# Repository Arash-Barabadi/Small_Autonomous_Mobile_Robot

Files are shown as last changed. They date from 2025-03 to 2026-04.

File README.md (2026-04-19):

# Small Autonomous Mobile Robot
### The first challenge is budgeting. I have already designed an architecture for a teleoperated car using ROS2 on a Jetson Orin NX, which is straightforward since the Jetson provides a powerful computing platform for compiling and executing all necessary code.
### To reduce costs, I opted to use a ESP32 as my main microcontroller, which costs only about €5 instead of €800!  The main limitation of the ESP32 is its lack of direct support for ROS2. However, it does support micro-ROS. Therefore, I decided to implement all the code within the micro-ROS framework.

[🎥 Watch my project demo on YouTube](https://www.youtube.com/watch?v=UUFdapDHFw0)



Robot_1st

Robot_2nd

# Networking (ESP32 ↔ ROS 2 PC)

## A guide how to intall micro-ros agent in our system is as follows:
## https://cps.unileoben.ac.at/install-micro-ros-on-esp32/
## This robot uses micro-ROS over WiFi (UDP). The ESP32 connects to a WiFi network and sends ROS 2 messages to the micro-ROS agent running on the PC.
## Architecture
### ESP32 publishes: /scan, /imu/data, /wheel_ticks, ....
### ESP32 subscribes: /cmd_vel, ...
### PC runs: micro_ros_agent (UDP on port 8888)
### Transport: WiFi UDP (udp4)
### Requirements: 1- ESP32 and PC must be on the same network, 2- ESP32 must be able to reach the PC IP, 3- Port 8888/UDP must not be blocked by firewall
## Home WiFi Setup (Router Network)
## A- (Microcontroller Side) ESP32 config

### Find PC IP: On Ubuntu:

```bash
ip a
```

### Note: Use the inet ... address under WiFi interface (usually wlp, e.g. inet 10.126.78.187/24 brd 10.126.78.255 scope global dynamic noprefixroute wlp0s20f3). Example output:
```bash
inet 10.126.78.187/24 brd 10.126.78.255 scope global dynamic noprefixroute wlp0s20f3
```
### In main.cpp:
```cpp
char ssid[]     = "YOUR_WIFI_NAME";
char password[] = "YOUR_WIFI_PASSWORD";
IPAddress agent_ip(10, 126, 78, 187);   // PC IP on the same WiFi
const uint16_t agent_port = 8888;
```

## B- (PC side) Start micro-ROS agent
```bash
ros2 run micro_ros_agent micro_ros_agent udp4 --port 8888
```

Verify through :
```bash
ros2 topic list
ros2 topic echo /scan --once
```

# TF:



## System Overview
### Sensors & Sources
#### - Wheel encoders → wheel odometry node → /odom + odom → base_link TF
#### - LD14P LiDAR → micro-ROS → /scan (frame_id: base_laser)
### Static TF:
#### - base_link → base_laser
#### - base_link → imu_link
## SLAM
###  Package: slam_toolbox
###  Mode: online_async
### Frames: map → odom → base_link → base_laser

## Terminal Commands Used (ubuntu)
### 1- Start the micro-ROS Agent (UDP over Wi-Fi)
```bash
ros2 run micro_ros_agent micro_ros_agent udp4 --port 8888
```
### 2- Teleoperation - We can drive it with the standard ROS 2 keyboard teleop that publishes geometry_msgs/Twist (think of it like format of coommand) on /cmd_vel, our robot will subscribe to /cmd_vel (think of it like the channel where the command is sent) and moves accordingly. 

```bash
ros2 run teleop_twist_keyboard teleop_twist_keyboard
```
### 3- Static Transforms
#### Base  → Lidar (unit meter, radian)

```bash
ros2 run tf2_ros static_transform_publisher   --x 0 --y 0 --z 0.04125   --roll 0 --pitch 0 --yaw 0   --frame-id base_link --child-frame-id base_laser
```
#### Base → IMU (unit meter, radian)

```bash
ros2 run tf2_ros static_transform_publisher --x -0.0674 --y 0.006355 --z -0.0053 --roll 0 --pitch 0  --yaw -1.57 --frame-id base_link --child-frame-id imu_link
```
### 4- Wheel Odometry Node

```bashr
ros2 run wheel_odometry wheel_odometry_node
```

### 5- SLAM (slam_toolbox)
```bash
ros2 launch slam_toolbox online_async_launch.py slam_params_file:=/home/$USER/ros2_ws/src/wheel_odometry/config/slam_params.yaml
```
### 6- RVIZ

```bash
rviz2 -d /opt/ros/jazzy/share/nav2_bringup/rviz/nav2_default_view.rviz
```
### 7- Navigation
```bash
// ros2 launch nav2_bringup navigation_launch.py use_sim_time:=false params_file:=/home/$USER/ros2_ws/src/wheel_odometry/config/nav2_params.yaml
ros2 launch wheel_odometry navigation.launch.py map:=/home/arash/ros2_ws/maps/test_map.yaml

ros2 topic pub --once /initialpose geometry_msgs/msg/PoseWithCovarianceStamped "{
  header: {frame_id: 'map'},
  pose: {
    pose: {
      position: {x: 0.0, y: 0.0, z: 0.0},
      orientation: {z: 0.0, w: 1.0}
    },
    covariance: [0.25, 0.0, 0.0, 0.0, 0.0, 0.0,
                 0.0, 0.25, 0.0, 0.0, 0.0, 0.0,
}"}              0.0, 0.0, 0.0, 0.0, 0.0, 0.5]

```

# Challenges
## Challenges accomplished
## __ Pure rotation fix __

### During testing, the robot could move forward and turn while moving, but it could not rotate in place with a pure angular command like:

```bash
ros2 topic pub /cmd_vel geometry_msgs/msg/Twist "{linear: {x: 0.0}, angular: {z: 2.0}}" -r 5
```
### Interestingly, rotation worked as soon as a very small forward velocity was added, for example:

```bash
ros2 topic pub /cmd_vel geometry_msgs/msg/Twist "{linear: {x: 0.02}, angular: {z: 2.0}}" -r 5
```
### This showed that the issue was not in ROS 2 communication, but in the drivetrain behavior: pure in-place rotation was not overcoming static friction.
### Fix: A small internal linear assist was added inside cmdVelCallback() for pure rotation commands, before deadzone compensation:
``` cpp
if (fabsf(v) < 0.001f && fabsf(w) > 0.0f) {
  v = ROTATION_ASSIST_LINEAR;
}

v = compensateLinearDeadzone(v);
w = compensateAngularDeadzone(w);
```
### with
``` cpp
static constexpr float ROTATION_ASSIST_LINEAR = 0.02f;
```
### Result : After this change, pure rotation worked reliably.

## __ Watch dog __
## My first aim is to drive the robot over Wi-Fi communication between my laptop and the ESP32. I’ll use PlatformIO for building, testing, and deploying code on the ESP32, as it is a better alternative to the Arduino IDE. PlatformIO is installed on VS Code.

### 1- Originally, the robot continued moving indefinitely if no new /cmd_vel message was received (for example, when the Wi-Fi connection dropped or the teleop node stopped). This caused unsafe behavior — the last velocity command remained active and the robot kept accelerating or turning without control. 
### To solve this, a command timeout WATCHDOG was implemented. It continuously checks the time since the last received command and automatically stops both motors if no new command arrives within 250 ms as below:
```cpp
// =============== Update timestamp whenever a command arrives ========================
void cmdVelCallback(const void *msgin) {
  
  // at first update and record timestamp as soon as receiving a message
  last_cmd_us = micros();  // micros() returns the current time in microseconds

  //The incoming message is cast to a geometry_msgs::msg::Twist type
  const auto *msg = (const geometry_msgs__msg__Twist *)msgin;

  float v = constrain(msg->linear.x  / MAX_V, -1.0f, 1.0f);
  float w = constrain(msg->angular.z / MAX_W, -1.0f, 1.0f);

  float left_norm  = (v - w * TRACK / 2.0f) * K_LEFT;
  float right_norm = (v + w * TRACK / 2.0f) * K_RIGHT;

  setMotor(L_IN1, L_IN2, 0, speedToPwm(left_norm));
  setMotor(R_IN1, R_IN2, 1, speedToPwm(right_norm));
}
// ================== Check timeout each loop ======================
void checkCmdTimeout() {
  uint32_t now = micros();
  if (last_cmd_us && (now - last_cmd_us > CMD_TIMEOUT_US)) {
    safetyStop();
  }
}

```

### 2- The LD14P LiDAR outputs scan data using a clockwise angle convention and a left-handed coordinate system, which does not match the ROS REP-103 standard (counter-clockwise, right-handed). This mismatch caused mirrored scans and incorrect visualization in RViz and SLAM. To fix this, the LiDAR angle interpretation was corrected directly inside main.cpp on the ESP32 instead of trying to compensate with TF. Each raw LD14 angle is converted using θ_ros = −θ_ld14, ensuring the scan follows the ROS counter-clockwise convention. The LaserScan beam indexing and angle range were also updated to [-π, π], allowing the LiDAR to behave like a standard ROS sensor while TF now only represents the physical mounting of the LiDAR.
```cpp
/// The scan was redefined to cover a full ROS-style range:
static constexpr float ANGLE_MIN_RAD = -PI;
static constexpr float ANGLE_MAX_RAD =  PI;
static constexpr float ANGLE_INC_RAD = (2 * PI) / SCAN_BEAMS;
/// Added helper function for angle conversion
/// This performs the critical transformation: clockwise  → counter-clockwise & left-handed → right-handed
static inline float ld14DegToRosRad(float angle_deg_ld14)
{
    float angle_rad_ld14 = angle_deg_ld14 * DEG2RAD;
    float angle_rad_ros  = -angle_rad_ld14;
    return wrapToPi(angle_rad_ros);
}
/// Inside lidarSpinOnce() each raw LD14 point is converted before assigning it to a LaserScan beam:
float angle_rad_ros = ld14DegToRosRad(angle_deg_ld14);

float beam_f = (angle_rad_ros - ANGLE_MIN_RAD) / ANGLE_INC_RAD;
int beam = lroundf(beam_f);

/// Unobserved scan beams are filled with INFINITY:

scan_ranges[i] = INFINITY;

```

### https://www.linkedin.com/posts/prof-dr-ing-lars-n-josler-b35999161_robotics-engineering-opensource-share-7448631464512032768-y-hW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

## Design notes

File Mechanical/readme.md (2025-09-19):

# Caster Wheel Spacer
### as the robot needs to be stable, it's decks are requred to be parrallel to the ground. For this I needed to design a simple spacer beteen caster wheel and the deck to compensate this height difference:
### The 3D printed spacer:


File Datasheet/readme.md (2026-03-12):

## Slam explanation:

## https://husarion.com/tutorials/ros2-tutorials/8-slam/

## Some guides:
## https://micro.ros.org/
## https://robofoundry.medium.com/
## https://robofoundry.medium.com/building-cheapest-ros2-robot-using-esp32-part-1-hardware-build-af0044de68ce

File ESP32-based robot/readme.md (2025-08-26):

## ESP32S_WROOM-32



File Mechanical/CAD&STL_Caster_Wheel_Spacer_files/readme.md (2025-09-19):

# Caster Wheel Spacer
### As the robot needs to be stable, its decks must be parallel to the ground. For this, I designed a simple spacer between the caster wheel and the deck to compensate for the height difference.


### The 3D printed spacer:


### Before using spacer:


### After using spacer:


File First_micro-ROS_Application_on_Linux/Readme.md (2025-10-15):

# Step 1: Install ROS 2 and micro-ROS Build System
# Micro-ROS 
## The ROS framework, which can be considered quite large, needs to be brought onto the microcontroller. This goal can be achieved using the micro-ROS framework, which my robot is based on.
### ROS2 installation: 
### Please refer to the following website: https://docs.ros.org/en/foxy/Installation/Ubuntu-Install-Debians.html for installing ROS2 humble.
### Micro-Ros installation: 
### 1- Source the ROS 2 installation
```bash 
source /opt/ros/$ROS_DISTRO/setup.bash
```
### 2- Create a workspace and download the micro-ROS tools
```bash
mkdir microros_ws
cd microros_ws
git clone -b $ROS_DISTRO https://github.com/micro-ROS/micro_ros_setup.git src/micro_ros_setup
```

### 3- Update dependencies using rosdep
```bash
sudo apt update && rosdep update
rosdep install --from-paths src --ignore-src -y
```

### 4- Install pip
```bash
sudo apt-get install python3-pip
```

### 5- Build micro-ROS tools and source them
```bash
colcon build
source install/local_setup.bash
```
# Step 2: Understand the micro-ROS Build System Workflow

## The micro-ROS build system consists of four steps:

###    1-Create – Downloads required code repositories and cross-compilation toolchains.
#### ***Cross-compilation is the process of compiling code on one system (the host: Our Computer) to run on a different system (the target:here Raspberry Pi Pico) that may have a different architecture, operating system, or environment.***

##### For example: You write and compile code on your Ubuntu PC (x86_64).The compiled binary is meant to run on a microcontroller (Raspberry Pi Pico).

### Since the microcontroller may lack the necessary resources (CPU, memory, OS) to run a full compiler, cross-compilation allows you to generate compatible binaries on your powerful development machine.

###    2-Configure – Selects the app, transport method, and agent details.
###    3-Build – Cross-compiles the selected app.
###    4-Flash – Installs the compiled binaries on the hardware.

# Step 3: Create a Firmware Workspace

## Create the firmware workspace:
```bash
ros2 run micro_ros_setup create_firmware_ws.sh host
```
### A new firmware/ folder is created, containing:

###    main.c: Application logic & CMakeLists.txt: Compilation script

# Step 4: Configure the Ping Pong Application

##    Locate the built-in ping_pong app:
```bash
microros_ws/src/uros/micro-ROS-demos/rclc/ping_pong
```

### The app has two publisher-subscriber pairs:

###    A ping publisher sends unique ping messages.
###    A ping subscriber listens for external pings.
###    A pong publisher responds when a ping is received.

# Step 5: Build the Firmware

## Since micro-ROS is running on Linux (not a microcontroller), no cross-compilation is needed. Build the firmware:
```bash
ros2 run micro_ros_setup build_firmware.sh
source install/local_setup.bash
```
# Step 6: Create and Build the micro-ROS Agent

##    Download the micro-ROS agent packages:
```bash
ros2 run micro_ros_setup create_agent_ws.sh
```
## Build the agent:
```bash
ros2 run micro_ros_setup build_agent.sh
source install/local_setup.bash
```

### What is the micro-ROS Agent? 🤖📡

#### The micro-ROS Agent is like a translator or middleman between micro-ROS nodes (running on tiny devices or a Linux system) and the main ROS 2 network.
#### 🔹 Role of micro-ROS Agent

####    Microcontrollers (tiny computers) can't directly communicate with a full ROS 2 system.
####    The micro-ROS Agent acts as a bridge between:
####        micro-ROS nodes (running on embedded devices or Linux).
####        ROS 2 nodes (running on a standard computer).
####    It receives messages from micro-ROS nodes and forwards them to ROS 2, and vice versa.

#### 💡 Think of it like an interpreter 🗣️
#### Imagine a person speaking English (ROS 2) and another speaking Spanish (micro-ROS). The micro-ROS Agent is the interpreter who helps them understand each other.

# Step 7: Run the micro-ROS Application

##    Start the micro-ROS agent:
```bash
ros2 run micro_ros_agent micro_ros_agent udp4 --port 8888
```
## Open another terminal and start the micro-ROS node:
```bash
source /opt/ros/$ROS_DISTRO/setup.bash
source install/local_setup.bash
export RMW_IMPLEMENTATION=rmw_microxrcedds
ros2 run micro_ros_demos_rclc ping_pong
```

# Step 8: Test the Application
##  8.1 Verify the Ping Messages

##  Now, we want to check that everything is working. Open a new command line. We are going to listen to the ping topic with ROS 2 to check whether the micro-ROS Ping Pong node is correctly publishing the expected pings:

```bash
ros2 topic echo /microROS/ping
```

##  Expected output(we should see the topic messages published by the Ping Pong node every 5 seconds):
```bash
    stamp:
      sec: 20
      nanosec: 867000000
    frame_id: '1344887256_1085377743'
    ---
```
## At this point, we know that our app is publishing pings. 
## Let’s check if it also answers to someone else’s pings. If this works, it’ll publish a pong. So, first of all, let’s subscribe with ROS 2 to the pong topic from a new shell (notice that initially we don’t expect to receive any pong, since none has been sent yet):

##    Open a new terminal and listen to the /microROS/pong topic:
```bash
ros2 topic echo /microROS/pong
```
##  8.2 And now, let’s publish a fake_ping with ROS 2 from yet another command line and Verify Pong Response:
```bash
ros2 topic pub --once /microROS/ping std_msgs/msg/Header '{frame_id: "fake_ping"}'
```
## Now, we should see this fake_ping in the ping subscriber console, along with the micro-ROS pings:
```bash
user@user:~$ ros2 topic echo /microROS/ping
stamp:
  sec: 0
  nanosec: 0
frame_id: fake_ping
---
stamp:
  sec: 305
  nanosec: 973000000
frame_id: '451230256_1085377743'
---
stamp:
  sec: 310
  nanosec: 957000000
frame_id: '2084670932_1085377743'
---
```
## Also, we expect that, because of having received the fake_ping, the micro-ROS node will answer with a pong:
```bash
user@user:~$ ros2 run micro_ros_demos_rcl ping_pong
Ping send seq 1706097268_1085377743
Ping send seq 181171802_1085377743
Ping send seq 1385567526_1085377743
Ping send seq 926583793_1085377743
Ping send seq 1831510138_1085377743
Ping received with seq fake_ping. Answering.
Ping send seq 1508705084_1085377743
Ping send seq 1702133625_1085377743
Ping send seq 176104820_1085377743
```
## As a consequence, in the pong subscriber console, we should see the micro-ROS app answer to our fake_ping:
```bash
user@user:~$ ros2 topic echo /microROS/pong
stamp:
  sec: 0
  nanosec: 0
frame_id: fake_ping
---
```
# Step 9: Run Multiple Ping Pong Nodes

##    No Extra Hardware Required – Unlike embedded systems, where each micro-ROS node would typically run on a separate microcontroller or board, Linux allows you to simulate multiple micro-ROS nodes on the same machine.

##    Multi-Node Testing – You can run multiple instances of the ping_pong application in different terminals, each acting as an independent micro-ROS node. This helps simulate and test real-world scenarios where multiple nodes communicate.

##    Using the Same micro-ROS Agent – Since micro-ROS nodes need an agent to communicate with ROS 2, all instances can share the same running agent, reducing setup complexity.

##    Practical Testing Method – By opening four different terminals, each running a separate instance of the ping_pong node, you can observe how they interact with each other in a simulated multi-node environment.

##    What Happens in Practice?

###    When multiple instances of the ping_pong node run:

####        1-Each instance sends pings with a unique identifier.
####        2-Other instances respond with pongs, mimicking communication between independent micro-ROS devices.
####        3-This allows for debugging and performance evaluation without needing multiple physical devices.
## One of the advantages of having a Linux micro-ROS app is that you don’t need to buy a bunch of hardware in order to test some multi-node micro-ROS apps. So, with the same micro-ROS agent of the last section, let’s open four different command lines and run the following on each

```bash
cd microros_ws

source /opt/ros/$ROS_DISTRO/setup.bash
source install/local_setup.bash

export RMW_IMPLEMENTATION=rmw_microxrcedds

ros2 run micro_ros_demos_rclc ping_pong
```
## As soon as all micro-ROS nodes are up and connected to the micro-ROS agent you will see them interacting:
```bash
user@user:~$ ros2 run micro_ros_demos_rclc ping_pong
Ping send seq 1711620172_1742614911                         <---- This micro-ROS node sends a ping with ping ID "1711620172" and node ID "1742614911"
Pong for seq 1711620172_1742614911 (1)                      <---- The first mate pongs my ping
Pong for seq 1711620172_1742614911 (2)                      <---- The second mate pongs my ping
Pong for seq 1711620172_1742614911 (3)                      <---- The third mate pongs my ping
Ping received with seq 1845948271_546591567. Answering.     <---- A ping is received from a mate identified as "546591567", let's pong it.
Ping received with seq 232977719_1681483056. Answering.     <---- A ping is received from a mate identified as "1681483056", let's pong it.
Ping received with seq 1134264528_1107823050. Answering.    <---- A ping is received from a mate identified as "1107823050", let's pong it.
Ping send seq 324239260_1742614911
Pong for seq 324239260_1742614911 (1)
Pong for seq 324239260_1742614911 (2)
Pong for seq 324239260_1742614911 (3)
Ping received with seq 1435780593_546591567. Answering.
Ping received with seq 2034268578_1681483056. Answering.
```

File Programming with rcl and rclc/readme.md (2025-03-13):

## This section is about micro-ROS C API : rclc , (which helps us write micro-ROS programs easily)

###    Similar to ROS2: The main building blocks (like publishers, subscribers, services, and timers) work the same way in micro-ROS as they do in regular ROS2.
###    Built on ROS2 Core: micro-ROS uses the same ROS2 client library (rcl) as standard ROS2.
###    rclc Makes It Easier: The rclc package doesn’t change how things work—it just provides helper functions to make writing micro-ROS programs simpler.
###    No Extra Layers: Unlike rclcpp (C++) or rclpy (Python), which add extra layers on top of rcl, rclc only introduces new features when absolutely necessary.
###    Executors: One new feature in rclc (in comparison to rcl) is the Executor, which helps manage multiple tasks efficiently.

## In short, rclc = micro-ROS version of rcl, but easier to use!

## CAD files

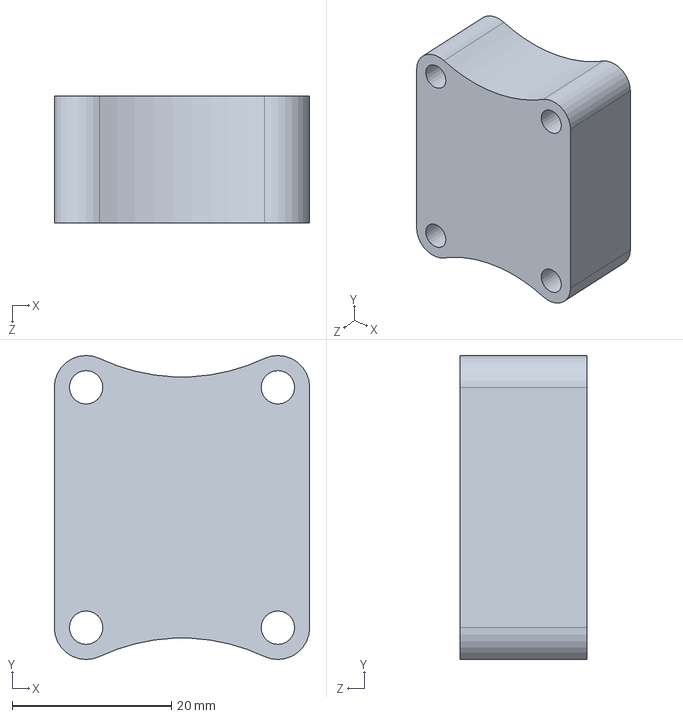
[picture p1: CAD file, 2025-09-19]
Mechanical/CAD&STL_Caster_Wheel_Spacer_files/Caster_Wheel_Spacer.SLDPRT
32.1 x 38.2 x 16.0 mm

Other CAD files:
Mechanical/CAD&STL_Caster_Wheel_Spacer_files/Caster_Wheel_Spacer.STL

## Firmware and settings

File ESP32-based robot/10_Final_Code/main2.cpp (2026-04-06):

// ============================= Standard and micro-ROS Libraries =============================
#include <Arduino.h>
#include <WiFi.h>
#include <micro_ros_platformio.h>
#include <math.h>
#include <Wire.h>
#include <Adafruit_BNO08x.h>
#include <rmw_microros/rmw_microros.h>

// ============================= ROS 2 Libraries =============================
#include <rcl/rcl.h>
#include <rclc/rclc.h>
#include <rclc/executor.h>

#include <geometry_msgs/msg/twist.h>
#include <sensor_msgs/msg/imu.h>
#include <std_msgs/msg/int32_multi_array.h>
#include <sensor_msgs/msg/laser_scan.h>
#include <builtin_interfaces/msg/time.h>

#ifndef INFINITY
#define INFINITY (1.0f / 0.0f)
#endif

// ============================= micro-ROS Agent IP and Port =============================
char ssid[]     = "FRITZ!Box 7560 IQ";
char password[] = "28715329684835834345";
IPAddress agent_ip(192, 168, 178, 164);
const uint16_t agent_port = 8888;

// ============================= Motor Driver Pin Definitions =============================
const int R_IN1 = 19;
const int R_IN2 = 18;
const int R_PWM = 17;

const int L_IN1 = 27;
const int L_IN2 = 26;
const int L_PWM = 14;

// ============================== Watchdog variables =====================================
static uint32_t last_cmd_us = 0;
static constexpr uint32_t CMD_TIMEOUT_US = 500000; // 500 ms

// ============================= Encoder Pin Definitions =============================
const int ENC_L_A = 34;
const int ENC_L_B = 32;
const int ENC_R_A = 35;
const int ENC_R_B = 33;

static constexpr bool INVERT_LEFT_DIR  = false;
static constexpr bool INVERT_RIGHT_DIR = false;

// ============================= Drive tuning ============================================
// Physical robot parameters
static constexpr float TRACK = 0.163f;   // wheel separation (m)
static constexpr float MAX_V = 0.50f;    // max linear command (m/s)
static constexpr float MAX_W = 2.00f;    // max angular command (rad/s)

// Robot-level command deadzone compensation
// Keep these moderate. Startup/hold PWM below is the main fix.
static constexpr float MIN_EFFECTIVE_LINEAR  = 0.12f;
static constexpr float MIN_EFFECTIVE_ANGULAR = 0.18f;

// Side scaling
static constexpr float K_LEFT  = 1.00f;
static constexpr float K_RIGHT = 1.00f;

// Wheel-side minimum PWM to overcome friction
static constexpr uint8_t MIN_DUTY_L_FWD = 55;
static constexpr uint8_t MIN_DUTY_L_REV = 100;
static constexpr uint8_t MIN_DUTY_R_FWD = 55;
static constexpr uint8_t MIN_DUTY_R_REV = 55;

// Very small command deadband
static constexpr float CMD_DEADBAND_LINEAR  = 0.01f;
static constexpr float CMD_DEADBAND_ANGULAR = 0.03f;

// PWM slew limiting
static constexpr int16_t MAX_PWM_STEP = 10;

// Startup boost / hold minimum to remove hesitation
static constexpr uint32_t START_BOOST_US = 120000; // 120 ms
static constexpr int16_t START_BOOST_L = 140;
static constexpr int16_t START_BOOST_R = 140;
static constexpr int16_t HOLD_MIN_L = 95;
static constexpr int16_t HOLD_MIN_R = 95;

// ============================= LiDAR (LD14P) =============================================
static constexpr int LIDAR_RX_PIN = 16;
static constexpr int LIDAR_TX_PIN = 4;

static constexpr uint8_t LIDAR_HEADER            = 0x54;
static constexpr int     LIDAR_POINTS_PER_PACKET = 12;

static constexpr int   SCAN_BEAMS   = 720;
static constexpr float PI_F         = 3.14159265f;
static constexpr float TWO_PI_F     = 2.0f * PI_F;
static constexpr float DEG2RAD_F    = PI_F / 180.0f;

static constexpr float ANGLE_MIN_RAD = -PI_F;
static constexpr float ANGLE_INC_RAD = TWO_PI_F / SCAN_BEAMS;
static constexpr float ANGLE_MAX_RAD = ANGLE_MIN_RAD + ANGLE_INC_RAD * (SCAN_BEAMS - 1);

// ============================= BNO085 IMU ================================================
#define BNO08X_RESET -1
Adafruit_BNO08x bno08x(BNO08X_RESET);
sh2_SensorValue_t bno_sensor_value;

static constexpr uint32_t BNO_REPORT_US = 10000;  // 100 Hz
static constexpr sh2_SensorId_t ORI_REPORT = SH2_ROTATION_VECTOR;

struct BnoImuData {
  float qx = 0.0f;
  float qy = 0.0f;
  float qz = 0.0f;
  float qw = 1.0f;

  float gx = 0.0f;
  float gy = 0.0f;
  float gz = 0.0f;

  float ax = 0.0f;
  float ay = 0.0f;
  float az = 0.0f;
};

BnoImuData latest_imu;

// ============================= micro-ROS Entities =======================================
rcl_subscription_t cmd_vel_sub;
geometry_msgs__msg__Twist cmd_vel_msg;

rclc_executor_t executor;
rclc_support_t  support;
rcl_node_t      node;
rcl_allocator_t allocator;

// IMU publisher + timer
rcl_publisher_t imu_pub;
sensor_msgs__msg__Imu imu_msg;
rcl_timer_t imu_timer;

// Encoder ticks publisher + timer
rcl_publisher_t ticks_pub;
std_msgs__msg__Int32MultiArray ticks_msg;
rcl_timer_t ticks_timer;
static int32_t wheel_ticks_buf[2] = {0, 0};

// LiDAR LaserScan publisher
rcl_publisher_t scan_pub;
sensor_msgs__msg__LaserScan scan_msg;
static float scan_ranges[SCAN_BEAMS];
static float scan_intensities[SCAN_BEAMS];
static bool  scan_valid[SCAN_BEAMS];
static bool  lidar_first_frame    = true;
static float lidar_last_start_deg = 0.0f;
static int   lidar_frames_in_scan = 0;

// ============================ Error Checking Macros ======================================
#define RCCHECK(fn)     { if ((fn) != RCL_RET_OK) error_loop(); }
#define RCSOFTCHECK(fn) { rcl_ret_t _rc = (fn); (void)_rc; }

// ============================= Runtime motor state =======================================
static int16_t current_left_pwm   = 0;
static int16_t current_right_pwm  = 0;
static int16_t target_left_pwm    = 0;
static int16_t target_right_pwm   = 0;

static bool drive_active = false;
static uint32_t drive_boost_until_us = 0;

// ============================= Encoder counters ==========================================
volatile int32_t left_ticks  = 0;
volatile int32_t right_ticks = 0;

// ============================= Helper: sign ==============================================
static inline float signf_local(float x) {
  if (x > 0.0f) return 1.0f;
  if (x < 0.0f) return -1.0f;
  return 0.0f;
}

// ============================= Helper: stamp with ROS time ===============================
static inline void stamp_now(builtin_interfaces__msg__Time *t)
{
  int64_t now_ns = rmw_uros_epoch_nanos();

  if (now_ns <= 0) {
    t->sec     = 0;
    t->nanosec = 0;
  } else {
    t->sec     = (int32_t)(now_ns / 1000000000LL);
    t->nanosec = (uint32_t)(now_ns % 1000000000LL);
  }
}

// ============================= LiDAR angle helpers =======================================
static inline float wrapToPi(float a)
{
  while (a >= PI_F)  a -= TWO_PI_F;
  while (a < -PI_F)  a += TWO_PI_F;
  return a;
}

static inline float ld14DegToRosRad(float angle_deg_ld14)
{
  float angle_rad_ld14 = angle_deg_ld14 * DEG2RAD_F;
  float angle_rad_ros  = -angle_rad_ld14;
  return wrapToPi(angle_rad_ros);
}

// ================================= Motor drive ==========================================
void setMotorRaw(int in1, int in2, int pwm_chan, int16_t speed_pwm, bool brake_on_zero) {
  uint8_t duty = (uint8_t)constrain((int)abs(speed_pwm), 0, 255);

  if (speed_pwm > 0) {
    digitalWrite(in1, HIGH);
    digitalWrite(in2, LOW);
  } else if (speed_pwm < 0) {
    digitalWrite(in1, LOW);
    digitalWrite(in2, HIGH);
  } else {
    if (brake_on_zero) {
      digitalWrite(in1, HIGH);
      digitalWrite(in2, HIGH);
    } else {
      digitalWrite(in1, LOW);
      digitalWrite(in2, LOW);
    }
  }

  ledcWrite(pwm_chan, duty);
}

static inline int16_t slewStep(int16_t current, int16_t target, int16_t max_step) {
  if (target > current + max_step) return current + max_step;
  if (target < current - max_step) return current - max_step;
  return target;
}

static inline int16_t applyHoldMinimum(int16_t pwm, int16_t hold_min) {
  if (pwm == 0) return 0;
  if (abs(pwm) < hold_min) {
    return (pwm > 0) ? hold_min : -hold_min;
  }
  return pwm;
}

static inline void applyMotorPwms(bool brake_on_zero = false) {
  uint32_t now_us = micros();

  bool want_motion = (target_left_pwm != 0 || target_right_pwm != 0);
  bool currently_stopped = (current_left_pwm == 0 && current_right_pwm == 0);

  if (want_motion && currently_stopped && !drive_active) {
    drive_active = true;
    drive_boost_until_us = now_us + START_BOOST_US;
  }

  if (!want_motion) {
    drive_active = false;
  }

  int16_t commanded_left  = target_left_pwm;
  int16_t commanded_right = target_right_pwm;

  // Startup boost
  if (drive_active && (int32_t)(drive_boost_until_us - now_us) > 0) {
    if (commanded_left != 0) {
      commanded_left = (commanded_left > 0) ? START_BOOST_L : -START_BOOST_L;
    }
    if (commanded_right != 0) {
      commanded_right = (commanded_right > 0) ? START_BOOST_R : -START_BOOST_R;
    }
  } else {
    // Hold minimum once moving
    commanded_left  = applyHoldMinimum(commanded_left, HOLD_MIN_L);
    commanded_right = applyHoldMinimum(commanded_right, HOLD_MIN_R);
  }

  current_left_pwm  = slewStep(current_left_pwm,  commanded_left,  MAX_PWM_STEP);
  current_right_pwm = slewStep(current_right_pwm, commanded_right, MAX_PWM_STEP);

  setMotorRaw(L_IN1, L_IN2, 0, current_left_pwm,  brake_on_zero);
  setMotorRaw(R_IN1, R_IN2, 1, current_right_pwm, brake_on_zero);
}

static inline void safetyStop() {
  target_left_pwm   = 0;
  target_right_pwm  = 0;
  current_left_pwm  = 0;
  current_right_pwm = 0;
  drive_active = false;
  drive_boost_until_us = 0;
  setMotorRaw(L_IN1, L_IN2, 0, 0, true);
  setMotorRaw(R_IN1, R_IN2, 1, 0, true);
}

void error_loop() {
  while (true) {
    safetyStop();
    delay(100);
  }
}

// Map normalized wheel demand [-1,1] to PWM with minimum duty compensation
static inline int16_t speedToPwmSide(float s_norm, bool is_left) {
  s_norm = constrain(s_norm, -1.0f, 1.0f);

  if (fabsf(s_norm) < 0.001f) {
    return 0;
  }

  uint8_t min_duty;
  if (is_left) {
    min_duty = (s_norm >= 0.0f) ? MIN_DUTY_L_FWD : MIN_DUTY_L_REV;
  } else {
    min_duty = (s_norm >= 0.0f) ? MIN_DUTY_R_FWD : MIN_DUTY_R_REV;
  }

  float mag = fabsf(s_norm);
  uint8_t duty = (uint8_t)(min_duty + mag * (255 - min_duty));

  return (s_norm >= 0.0f) ? (int16_t)duty : -(int16_t)duty;
}

// Deadzone compensation on commanded robot motion
static inline float compensateLinearDeadzone(float v) {
  if (fabsf(v) < CMD_DEADBAND_LINEAR) return 0.0f;
  if (fabsf(v) < MIN_EFFECTIVE_LINEAR) return signf_local(v) * MIN_EFFECTIVE_LINEAR;
  return v;
}

static inline float compensateAngularDeadzone(float w) {
  if (fabsf(w) < CMD_DEADBAND_ANGULAR) return 0.0f;
  if (fabsf(w) < MIN_EFFECTIVE_ANGULAR) return signf_local(w) * MIN_EFFECTIVE_ANGULAR;
  return w;
}

// ================================= cmd_vel callback =====================================
void cmdVelCallback(const void *msgin) {
  last_cmd_us = micros();

  const auto *msg = (const geometry_msgs__msg__Twist *)msgin;

  float v = constrain(msg->linear.x,  -MAX_V, MAX_V);
  float w = constrain(msg->angular.z, -MAX_W, MAX_W);

  v = compensateLinearDeadzone(v);
  w = compensateAngularDeadzone(w);

  float left_mps  = (v - w * TRACK / 2.0f) * K_LEFT;
  float right_mps = (v + w * TRACK / 2.0f) * K_RIGHT;

  float left_norm  = constrain(left_mps  / MAX_V, -1.0f, 1.0f);
  float right_norm = constrain(right_mps / MAX_V, -1.0f, 1.0f);

  target_left_pwm  = speedToPwmSide(left_norm,  true);
  target_right_pwm = speedToPwmSide(right_norm, false);

  Serial.print("cmd_raw v=");
  Serial.print(msg->linear.x, 4);
  Serial.print(" w=");
  Serial.print(msg->angular.z, 4);
  Serial.print(" | cmd_used v=");
  Serial.print(v, 4);
  Serial.print(" w=");
  Serial.print(w, 4);
  Serial.print(" | target_left_pwm=");
  Serial.print(target_left_pwm);
  Serial.print(" target_right_pwm=");
  Serial.println(target_right_pwm);
}

void checkCmdTimeout() {
  uint32_t now = micros();
  if (last_cmd_us != 0 && (uint32_t)(now - last_cmd_us) > CMD_TIMEOUT_US) {
    safetyStop();
    last_cmd_us = 0;
  }
}

// ============================= BNO085 helpers ============================================
bool bnoEnableReports() {
  bool ok = true;
  ok &= bno08x.enableReport(ORI_REPORT, BNO_REPORT_US);
  ok &= bno08x.enableReport(SH2_GYROSCOPE_CALIBRATED, BNO_REPORT_US);
  ok &= bno08x.enableReport(SH2_LINEAR_ACCELERATION, BNO_REPORT_US);
  return ok;
}

bool bnoInit() {
  if (!bno08x.begin_I2C()) {
    return false;
  }
  delay(100);
  return bnoEnableReports();
}

void bnoPoll() {
  while (bno08x.getSensorEvent(&bno_sensor_value)) {
    switch (bno_sensor_value.sensorId) {

      case SH2_ROTATION_VECTOR:
      case SH2_GAME_ROTATION_VECTOR:
        latest_imu.qx = bno_sensor_value.un.rotationVector.i;
        latest_imu.qy = bno_sensor_value.un.rotationVector.j;
        latest_imu.qz = bno_sensor_value.un.rotationVector.k;
        latest_imu.qw = bno_sensor_value.un.rotationVector.real;
        break;

      case SH2_GYROSCOPE_CALIBRATED:
        latest_imu.gx = bno_sensor_value.un.gyroscope.x;
        latest_imu.gy = bno_sensor_value.un.gyroscope.y;
        latest_imu.gz = bno_sensor_value.un.gyroscope.z;
        break;

      case SH2_LINEAR_ACCELERATION:
        latest_imu.ax = bno_sensor_value.un.linearAcceleration.x;
        latest_imu.ay = bno_sensor_value.un.linearAcceleration.y;
        latest_imu.az = bno_sensor_value.un.linearAcceleration.z;
        break;

      default:
        break;
    }
  }
}

void imuTimerCallback(rcl_timer_t*, int64_t) {
  bnoPoll();

  stamp_now(&imu_msg.header.stamp);

  imu_msg.orientation.x = latest_imu.qx;
  imu_msg.orientation.y = latest_imu.qy;
  imu_msg.orientation.z = latest_imu.qz;
  imu_msg.orientation.w = latest_imu.qw;

  imu_msg.angular_velocity.x = latest_imu.gx;
  imu_msg.angular_velocity.y = latest_imu.gy;
  imu_msg.angular_velocity.z = latest_imu.gz;

  imu_msg.linear_acceleration.x = latest_imu.ax;
  imu_msg.linear_acceleration.y = latest_imu.ay;
  imu_msg.linear_acceleration.z = latest_imu.az;

  for (int i = 0; i < 9; i++) {
    imu_msg.orientation_covariance[i] = 0.0;
    imu_msg.angular_velocity_covariance[i] = 0.0;
    imu_msg.linear_acceleration_covariance[i] = 0.0;
  }

  imu_msg.orientation_covariance[0] = 0.02;
  imu_msg.orientation_covariance[4] = 0.02;
  imu_msg.orientation_covariance[8] = 0.05;

  imu_msg.angular_velocity_covariance[0] = 0.01;
  imu_msg.angular_velocity_covariance[4] = 0.01;
  imu_msg.angular_velocity_covariance[8] = 0.01;

  imu_msg.linear_acceleration_covariance[0] = 0.10;
  imu_msg.linear_acceleration_covariance[4] = 0.10;
  imu_msg.linear_acceleration_covariance[8] = 0.10;

  RCSOFTCHECK(rcl_publish(&imu_pub, &imu_msg, NULL));
}

// ============================= LD14P minimal parser =====================================
struct __attribute__((packed)) LidarPoint {
  uint16_t distance;
  uint8_t  intensity;
};

struct __attribute__((packed)) LidarFrame {
  uint8_t  header;
  uint8_t  ver_len;
  uint16_t speed;
  uint16_t start_angle;
  LidarPoint point[LIDAR_POINTS_PER_PACKET];
  uint16_t end_angle;
  uint16_t timestamp;
  uint8_t  crc8;
};

bool lidarReadFrame(LidarFrame &frame) {
  while (Serial2.available() >= (int)sizeof(LidarFrame)) {
    int c = Serial2.read();
    if (c != LIDAR_HEADER) {
      continue;
    }
    frame.header = (uint8_t)c;

    size_t want = sizeof(LidarFrame) - 1;
    size_t got  = Serial2.readBytes(((uint8_t*)&frame) + 1, want);
    if (got != want) return false;

    if (frame.ver_len != 0x2C) continue;
    return true;
  }
  return false;
}

void lidarSpinOnce() {
  LidarFrame f;

  while (lidarReadFrame(f)) {
    float start_deg = f.start_angle * 0.01f;
    float end_deg   = f.end_angle   * 0.01f;

    if (!lidar_first_frame) {
      if ((start_deg + 5.0f) < lidar_last_start_deg && lidar_frames_in_scan > 0) {
        for (int i = 0; i < SCAN_BEAMS; ++i) {
          if (!scan_valid[i]) {
            scan_ranges[i]      = INFINITY;
            scan_intensities[i] = 0.0f;
          }
        }

        stamp_now(&scan_msg.header.stamp);

        scan_msg.ranges.size      = SCAN_BEAMS;
        scan_msg.intensities.size = SCAN_BEAMS;
        RCSOFTCHECK(rcl_publish(&scan_pub, &scan_msg, NULL));

        for (int i = 0; i < SCAN_BEAMS; ++i) {
          scan_valid[i] = false;
        }
        lidar_frames_in_scan = 0;
      }
    }

    lidar_first_frame    = false;
    lidar_last_start_deg = start_deg;
    lidar_frames_in_scan++;

    if (end_deg < start_deg) end_deg += 360.0f;
    float span_deg = end_deg - start_deg;

    for (int i = 0; i < LIDAR_POINTS_PER_PACKET; ++i) {
      float frac = (LIDAR_POINTS_PER_PACKET == 1)
                 ? 0.0f
                 : (float)i / (float)(LIDAR_POINTS_PER_PACKET - 1);

      float angle_deg_ld14 = start_deg + span_deg * frac;

      while (angle_deg_ld14 >= 360.0f) angle_deg_ld14 -= 360.0f;
      while (angle_deg_ld14 < 0.0f)    angle_deg_ld14 += 360.0f;

      float angle_rad_ros = ld14DegToRosRad(angle_deg_ld14);

      float beam_f = (angle_rad_ros - ANGLE_MIN_RAD) / ANGLE_INC_RAD;
      int beam = (int)lroundf(beam_f);

      if (beam == SCAN_BEAMS) beam = 0;
      if (beam < 0 || beam >= SCAN_BEAMS) continue;

      uint16_t d_mm = f.point[i].distance;
      if (d_mm == 0) continue;

      float d_m = d_mm * 0.001f;

      if (!scan_valid[beam] || d_m < scan_ranges[beam]) {
        scan_ranges[beam]      = d_m;
        scan_intensities[beam] = (float)f.point[i].intensity;
        scan_valid[beam]       = true;
      }
    }
  }
}

// ============================= Quadrature encoder (A/B) ================================
void IRAM_ATTR onLeftA() {
  bool b = digitalRead(ENC_L_B);
  int dir = b ? -1 : +1;
  if (INVERT_LEFT_DIR) dir = -dir;
  left_ticks += dir;
}

void IRAM_ATTR onRightA() {
  bool b = digitalRead(ENC_R_B);
  int dir = b ? -1 : +1;
  if (INVERT_RIGHT_DIR) dir = -dir;
  right_ticks += dir;
}

void ticksTimerCallback(rcl_timer_t*, int64_t) {
  noInterrupts();
  wheel_ticks_buf[0] = left_ticks;
  wheel_ticks_buf[1] = right_ticks;
  interrupts();

  RCSOFTCHECK(rcl_publish(&ticks_pub, &ticks_msg, NULL));
}
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
void loop() {
  // Process ROS callbacks
  RCSOFTCHECK(rclc_executor_spin_some(&executor, RCL_MS_TO_NS(10)));

  // Update motors every loop, not only when a new ROS message arrives
  applyMotorPwms(false);

  // Safety timeout
  checkCmdTimeout();

  // LiDAR parsing / publishing
  lidarSpinOnce();

  delay(2);
}

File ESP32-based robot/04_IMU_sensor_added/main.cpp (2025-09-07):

// ============================= Standard and micro-ROS Libraries =============================
#include <Arduino.h>
#include <WiFi.h>
#include <micro_ros_platformio.h>
#include <math.h>  // added for fabsf()

// [MOD] Added for I2C (MPU-6050)
#include <Wire.h>
// ============================= ROS 2 Libraries =============================
#include <rcl/rcl.h>
#include <rclc/rclc.h>
#include <rclc/executor.h>
#include <geometry_msgs/msg/twist.h>

// [MOD] Added IMU message
#include <sensor_msgs/msg/imu.h>
// ============================= Wi-Fi Credentials =============================

//An IP address (e.g., 192.168.178.164) identifies a device on the network (like PC).
// A port number (e.g., 8888) identifies a specific service or application running on that device.

// ============================= micro-ROS Agent IP and Port =============================
//Git fixed: changed from `const char*` to `char[]`
char ssid[] = "FRITZ!Box 7560 IQ";             // Replace with your Wi-Fi SSID
char password[] = "28715329684835834345";      // Replace with your Wi-Fi password
IPAddress agent_ip(192, 168, 178, 164);         // Your PC IP
const uint16_t agent_port = 8888;

// ============================= Motor Driver Pin Definitions =============================
const int R_IN1 = 19 ;
const int R_IN2 = 18;
const int R_PWM = 17;

const int L_IN1 = 27;
const int L_IN2 = 26;
const int L_PWM = 14 ;

// ---------- Added: tuning & normalization constants ----------
static constexpr float TRACK = 0.20f;     // wheel separation (m), adjust accordingly
static constexpr float MAX_V = 0.50f;     // m/s corresponding to "full-scale" forward command
static constexpr float MAX_W = 2.00f;     // rad/s corresponding to "full-scale" yaw command

// Per-wheel gain to trim straight driving (increase the slower side slightly)
static constexpr float K_LEFT  = 1.00f;
static constexpr float K_RIGHT = 1.00f;

// Minimum duty to overcome static friction (0..255). Raise if wheels hesitate at low speeds.
static constexpr uint8_t MIN_DUTY = 20;

// Small deadband on normalized speed commands
static constexpr float DEADBAND = 0.01f;

// ============================= ROS 2 micro-ROS Entities =============================
//We're preparing our robot to receive commands from ROS 2. To do that, we need a few "tools" from micro-ROS to: 

// What it is: your mailbox. 	You say: “Please deliver messages from topic cmd_vel to this mailbox.” 
//It doesn’t hold the message itself—it’s just the channel for subscription.
//Think of it as: "Tell micro-ROS what to listen to"
rcl_subscription_t cmd_vel_sub;

// What it is: This is the actual message content (e.g., linear and angular velocity).
// Think of it as: "Stores the contents of the message received"
geometry_msgs__msg__Twist cmd_vel_msg;

// What it is: A helper that checks for new messages and calls the right function when one arrives.
// Think of it as: "The smart assistant that listens and reacts when new commands come in."
rclc_executor_t executor;

// What it is: A setup tool that initializes the whole ROS 2 communication system on your ESP32.
// Think of it as: "The person who sets up the communication environment for you."
rclc_support_t support;


// What it is: Your robot’s identity in the ROS 2 world.
// In this case: The node might be named "esp32_diffdrive".
// Think of it as: "This is me, the robot, talking in the ROS 2 network."
rcl_node_t node;

//What it is: A tool that handles memory allocation in micro-ROS (required for internal structures).
//Think of it as: "The memory manager that decides where things get stored."
rcl_allocator_t allocator;

// IMU publisher + timer
rcl_publisher_t imu_pub;
sensor_msgs__msg__Imu imu_msg;
rcl_timer_t imu_timer;

// ============================= Error Checking Macros =============================
// This macro checks if a function (fn) was successful, and if not, it enters an infinite error loop.
#define RCCHECK(fn) { if ((fn) != RCL_RET_OK) error_loop(); }

// This macro calls a function and stores the result, but it doesn’t check for errors or take action. It's used for non-critical operations.
#define RCSOFTCHECK(fn) { rcl_ret_t _rc = (fn); (void)_rc; }

// ============================= Error Loop Function =============================
void error_loop() {
  while (true) delay(100);
}

// ---------- Added: helper to map normalized speed [-1,1] to signed PWM with deadband & MIN_DUTY ----------
static inline int16_t speedToPwm(float s_norm) {
  // Clamp to [-1,1] and apply small deadband
  if (s_norm >  1.0f) s_norm =  1.0f;
  if (s_norm < -1.0f) s_norm = -1.0f;
  if (fabsf(s_norm) < DEADBAND) return 0;

  // Scale magnitude to [MIN_DUTY..255]
  float mag = fabsf(s_norm);
  uint8_t duty = (uint8_t)(MIN_DUTY + mag * (255 - MIN_DUTY));
  return (s_norm >= 0.0f) ? (int16_t)duty : -(int16_t)duty;
}

// ============================= Set Motor Speed and Direction =============================

// Function to set motor direction and speed using two digital pins and one PWM channel
// ---------- Note: updated to take signed PWM in range [-255..255] ----------
void setMotor(int in1, int in2, int pwm_chan, int16_t speed_pwm) {

  // Calculate the PWM duty cycle: 
  // Take the absolute value of speed (so negative speed doesn’t break it),
  // Clamp it between 0 and 255 to stay within 8-bit limits,
  // Convert the result to an unsigned 8-bit integer (0–255)
  uint8_t duty = (uint8_t)constrain((int)abs(speed_pwm), 0, 255);
  
  // Set motor direction:

  // If speed is positive, motor moves forward (IN1 = HIGH, IN2 = LOW)
  if (speed_pwm > 0) {
    digitalWrite(in1, HIGH); digitalWrite(in2, LOW);
  
  // If speed is negative, motor moves in reverse (IN1 = LOW, IN2 = HIGH)
  } else if (speed_pwm < 0) {
    digitalWrite(in1, LOW);  digitalWrite(in2, HIGH);
  
  // If speed is zero, stop the motor (both IN1 and IN2 LOW = brake or coast depending on driver)
  } else {
    digitalWrite(in1, LOW); digitalWrite(in2, LOW);
  }

  // Write the duty cycle to the selected PWM channel,
  // This controls how fast the motor spins (0 = off, 255 = full speed)
  ledcWrite(pwm_chan, duty);
}
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

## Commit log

2025-02-23 Rename raspberry-pi-pico-c-sdk.pdf to Raspberry Pi Pico-series C-C++ SDK-sdk.pdf
2025-09-07 Update repo with current folder contents
2026-02-10 Update WiFi credentials for ESP32
2026-02-10 Add platformio.ini for ESP32 project configuration
2026-02-15 Add Lidar data documentation
2026-02-19 Correct capitalization in README for ESP32 config
2026-02-19 Clarify ESP32 published and subscribed topics
    Updated published and subscribed topics for ESP32.
2026-03-11 Revise challenges section with detailed explanations
    Updated challenges section to include detailed explanations of the LiDAR angle correction and command timeout implementation.
